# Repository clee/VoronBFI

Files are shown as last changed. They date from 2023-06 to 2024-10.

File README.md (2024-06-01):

# BFI (Beefy Front Idlers)

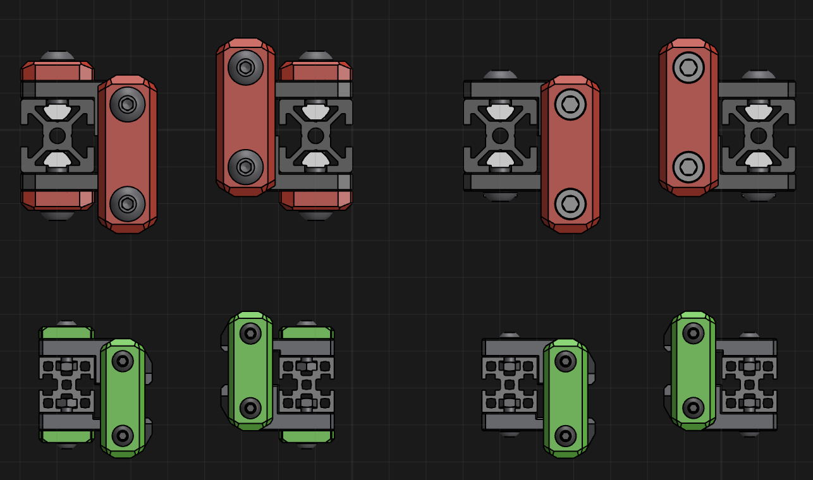
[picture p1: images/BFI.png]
BFI family render


### What?

These are replacement front idlers for Vorons (and Voron-based machines) designed with one core principle: use belt tension to *compress* printed layers instead of splitting or pulling them apart.

This design is available for Voron Trident, Voron 2.4, Salad Fork, and Micron.

### Why?

Using BFI means you should never have to deal with this kind of heartbreak again.

Stock | Rama's
--- | ---
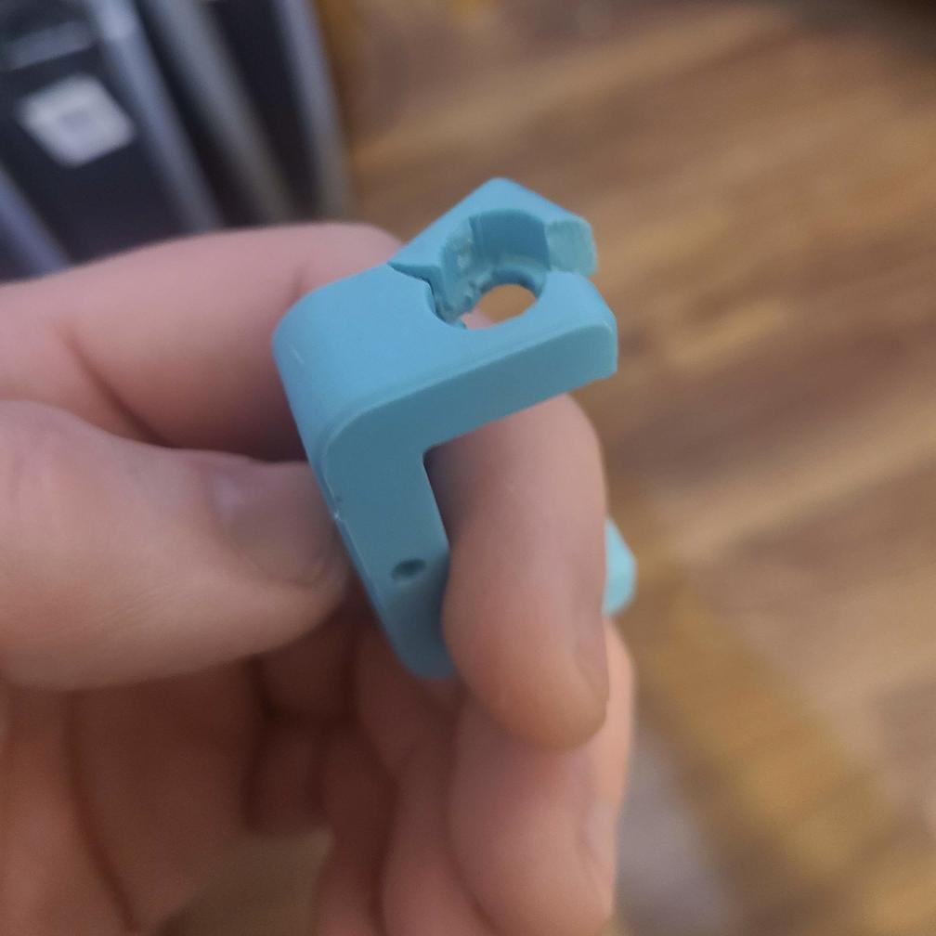
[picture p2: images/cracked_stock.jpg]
cracked stock front idler
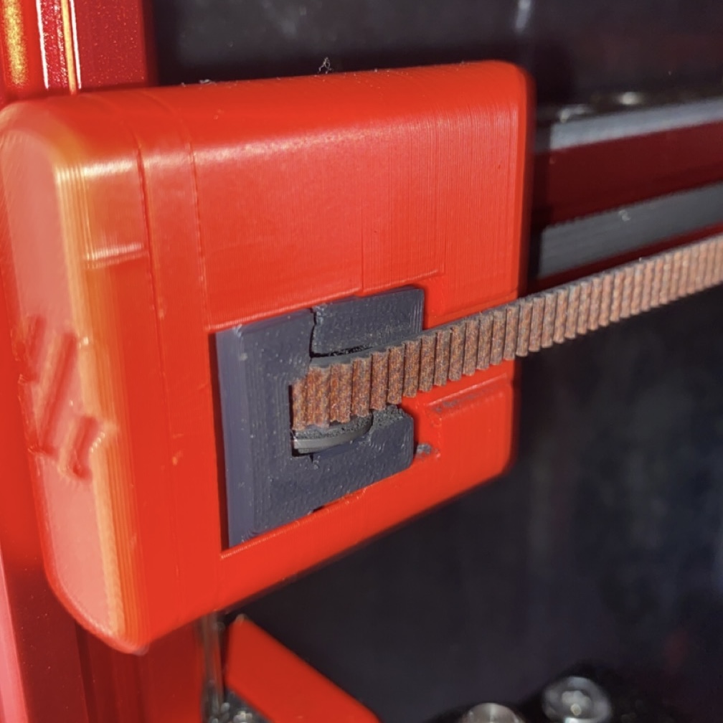
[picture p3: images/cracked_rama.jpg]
cracked Rama's front idler
 | 

## BFI for Trident

For Trident, you'll need:
- 4× M5×40 SHCS
- 4× M5 hex nuts
- 2× 5mm-diameter pin, 18mm long

...plus the same shim/bearing stack setup for each idler as the original stock front idlers.

## BFI for Voron 2.4

For V2.4, you'll need:
- 4× M5×30 BHCS 
- 4× M5 hex nuts
- 2× 5mm-diameter pin, 18mm long
- 2× M3 t-nuts
- 2× M3×16 BHCS

...plus the same shim/bearing stack setup for each idler as the original stock front idlers.

## BFI for Ants

For Salad Fork, you'll need:
- 4× M3×25 BHCS
- 4× standard Voron M3x5x4 heatset inserts (5mm outer diameter, 4mm deep)
- 2× M3×12 SHCS

For Micron, you'll need:
- 4× M3×20 BHCS
- 4× standard Voron M3x5x4 heatset inserts (5mm outer diameter, 4mm deep)
- 2× M3×12 SHCS

...plus the same shim/bearing stack setup for each idler as the original stock front idlers.

### But wait, there's more!

The same carriage design has also been applied to work with Micron, Voron 2.4, and Doomcube Z idlers.

# BZI (Beefy Z Idlers)

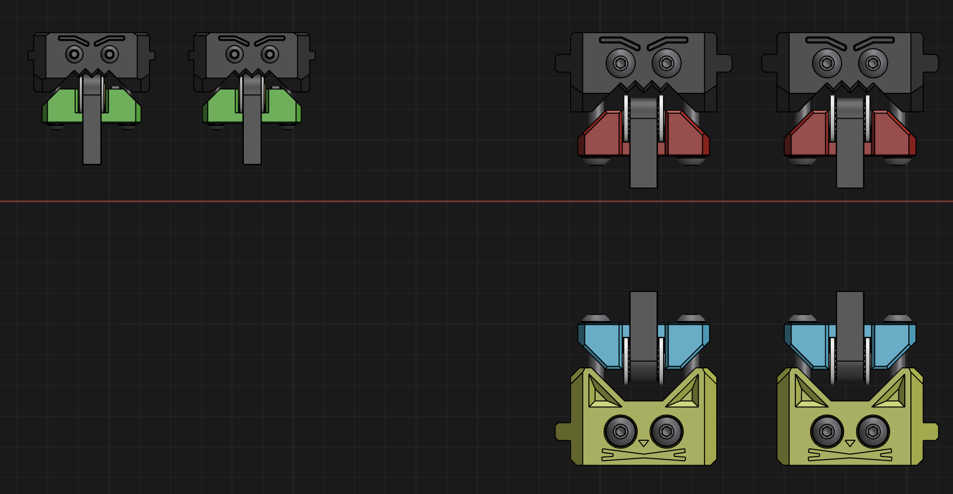
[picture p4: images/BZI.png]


## BZI for Voron 2.4

For V2.4, you'll need:
- 8× M5 hex nuts
- 8× M5×40 SHCS
- 4× 5mm-diameter pin, 22mm long

You'll reuse the existing M5×30 BHCS and roll-in M5 nuts for mounting to the frame, as well as the 20T toothed idlers from the original stock Z idlers.

## BZI for Micron

For Micron, you'll need: 
- 8× M3 hex nuts
- 8× M3×30 BHCS
- 4× M3×16 SHCS

You'll reuse the existing M3×20 BHCS and preloaded M3 hex nuts for mounting to the frame, as well as the shim/bearing stack setup from the original stock Z idlers.

## BZI for Doomcube

For Doomcube, you'll need:
- 8× M5 hex nuts
- 8× M5×40 SHCS
- 4x 5mm-diameter pin, 22mm long

You'll reuse the existing M5×25 BHCS and roll-in M5 nuts for mounting to the frame, as well as the 20T toothed idlers from the original stock Z idlers.

## One more thing

There are also a bunch of [usermods](usermods/) for BFI. If you have non-Gates idlers, or you want Voron logos, or wish BFI were more symmetrical… might want to check them out!

# Whose fault is all this anyway?

- @clee, initial prototype
- @bythorsthunder, early feedback and testing
- @KayosMaker, first port to V2.4
- @hartk1213, Micron and Doom 

While not directly built upon it, this design is definitely inspired by @Ramalama2's front idlers.

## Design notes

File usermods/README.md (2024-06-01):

# BFI user mods

### Included in this repo:

| Creator | Title | Description |
| --- | --- | --- |
|telxoid|[V2.4 & Trident Front Logos](https://github.com/clee/VoronBFI/tree/main/usermods/telxoid)| BFI Front Logos with Voron Logos and Dual colour option.|
||[V2.4 & Trident Grippy Carrier](https://github.com/clee/VoronBFI/tree/main/usermods/telxoid)| Updated carrier to allow the shaft to push from the top/bottom rather than slot in.|
|Jadecky|[BZI for Micron Pin Mod](https://github.com/clee/VoronBFI/tree/main/usermods/Jadecky/STLs/Pin%20Mod_Micron/BZI)| Pin Mod for Micron BZI.|
||[BFI for Micron Pin Mod](https://github.com/clee/VoronBFI/tree/main/usermods/Jadecky/STLs/Pin%20Mod_Micron/BFI)| Pin Mod for Micron BFI|
||[BZI for Micron Non symmetrical Bodies](https://github.com/clee/VoronBFI/tree/main/usermods/Jadecky/STLs/Non%20Symmetrical%20BZI%20Idler%20Bodies)| Removed one of the ears on the exposed side of the body, purely aesthetic.|
|LillianaMirrors|[BZI For 14mm Pulleys (Chaoticlab Idlers)](https://github.com/clee/VoronBFI/tree/main/usermods/LillianaMirrors/)| Widened the BZI idler hole for 14mm pulleys, commonly used on the 2.4 Tool-less Z Idlers|
|GiulianoM|[BZI for DoomCube 4040](./GiulianoM/)| Extended idler bodies for use with a DoomCube built with 4040 frames.|
|Mosher|[BZI Light](https://github.com/clee/VoronBFI/tree/main/usermods/Mosher/BZI%20Light%20Idlers)| Slimmed down wersion of BZI uses shorter man body screws and 2x M3 for carrier. Great variety of versions.|
|MikeYankeeOscarBeta|[9MM BFI](./MikeYankeeOscarBeta/)| 9mm BFI. Using 5x22mm pins|
|Tetsu|[Symmetrical BFI](./Tetsu/Symetrical%20BFI/)| Symmetrical BFI parts with options for M3 & M5 hardware & BFI front logos|
|DonaldSayers|[45 Degree Housing](./DonaldSayers/)| Made the housing a bit easier to print the overhang. Mostly print aesthetics.

## Other BFI forks/variants
| Creator | Title | Description |
| --- | --- | --- |
| Radiotbo | [Smooth BFI](https://github.com/Radiotbo3d/SBFI) | Smoother, more symmetrical take on BFI for V2.4 and VT |
| Diyshift | [BFI Gears](https://github.com/Diyshift/3D-Printer/tree/main/BFI%20Gears) | Allows you to adjust both M5 bolts at once for VT |

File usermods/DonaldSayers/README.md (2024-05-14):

## V2.4 Housing with 45 degree overhang.
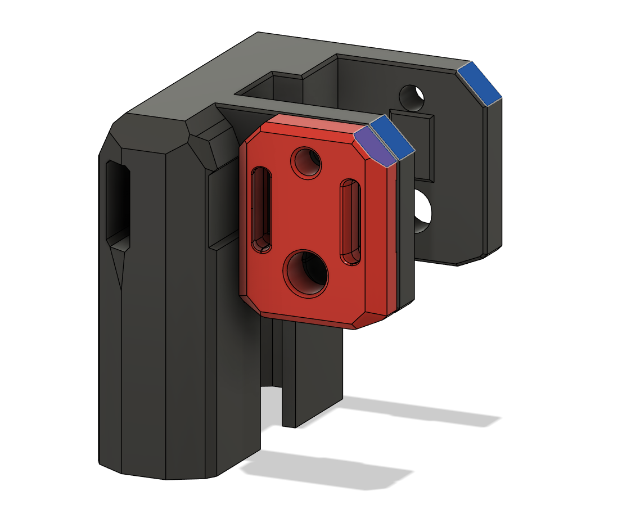
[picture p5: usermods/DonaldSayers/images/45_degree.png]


The angle on the housing was really steep. I cut it off and blended it with a chamfer to blend it in. It does make the default belt holder overhang on the back so I've added the same geometry to work with both A and B.

Mostly for print aesthetics.

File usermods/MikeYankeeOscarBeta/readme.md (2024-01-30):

## MikeYankeOscarBeta  Voron 2.4 9mm BFI for 9mm belts and 5x22mm pins
#### VoronDesign-Discord: MikeyMike V2.5796

Made to fit with the 9mm Belt mod XY idlers and AB stepper mounts found here: 
https://www.printables.com/model/485237-voron-24-9mm-gantry 
(which might also be this project on github: https://github.com/Sneeky-Pete/Fatso)

These replace the 9mm ramalama2 front idlers in the Etretti Voron 2.4 9mm gantry

## BFI 9mm belt mod for Voron 2.4

For V2.4 9mm BFI, you'll need:
- 4× M5×30 BHCS 
- 4× M5 hex nuts
- 2× 5mm-diameter pin, 22mm long
- 2× M3 t-nuts
- 2× M3×16 BHCS (i think, but might need longer)

...plus the 14mm shim/bearing stack setup for each idler, same as the 9mm belt mod front idlers.

## Kudos to the voron community, and especially:  
- clee for the BFI BZI mod
- Etretti &&|| Sneeky-Pete for the 9mm mod
- Johan/Alucardi V2.12171 V0.1479 for breaking his 9mm ramalama2 idlers

## Changelog:
- 20230910: initial version

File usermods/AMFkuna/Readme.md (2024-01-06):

Modified version of [telxoid](https://github.com/clee/VoronBFI/tree/main/usermods/telxoid) usermod of BFI for V2.4/Trident

M3 heat inserts and M3 fasteners for fine tunning

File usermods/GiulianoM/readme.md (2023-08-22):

# BZI Frame for DoomCube 4040
I'm making a DoomCube 2.4 variant with 4040 extrusions for the frame.

These are extended idler bodies to take advantage of the deeper 4040 extrusions.

They have a Cat *and* a Bird on them.

Modifications:
* Hex nuts are now in the middle of the body.
* You'll need 2x M5 50mm BHCS instead of 40mm.
* You'll need 2x extra M5 Roll In nuts and 2x extra M5 25mm BHCS.

## Pictures

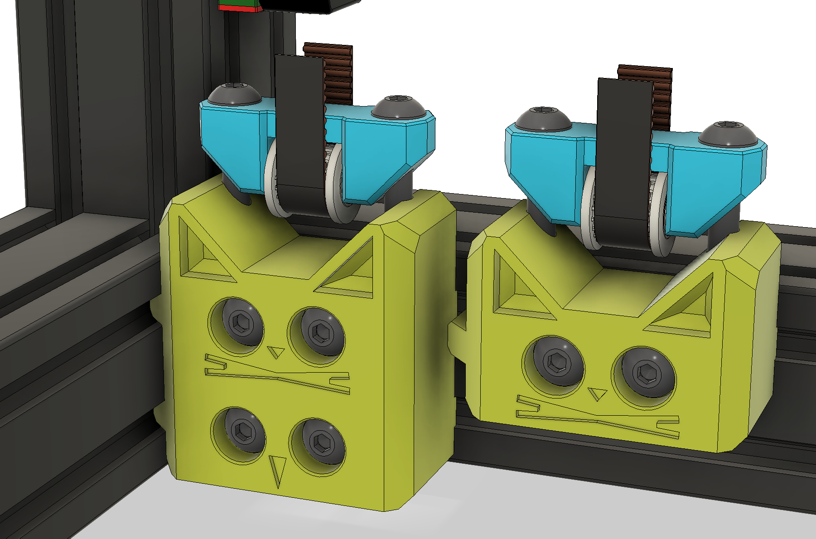
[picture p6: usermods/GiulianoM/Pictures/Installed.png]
Meow Meow


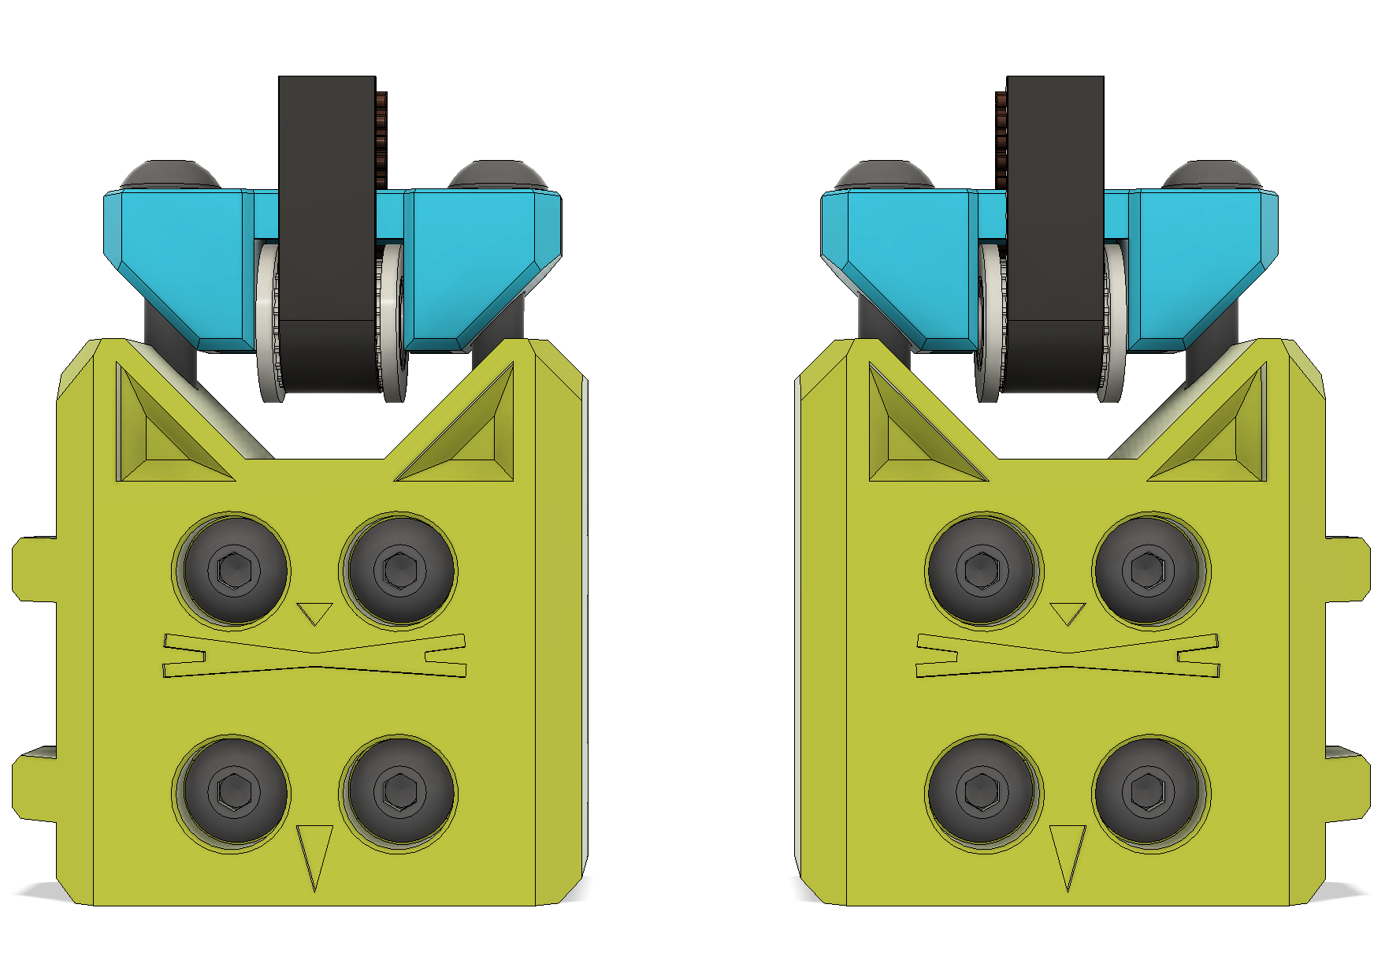
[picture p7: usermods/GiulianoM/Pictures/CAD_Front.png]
Meow Meow SQUAWK


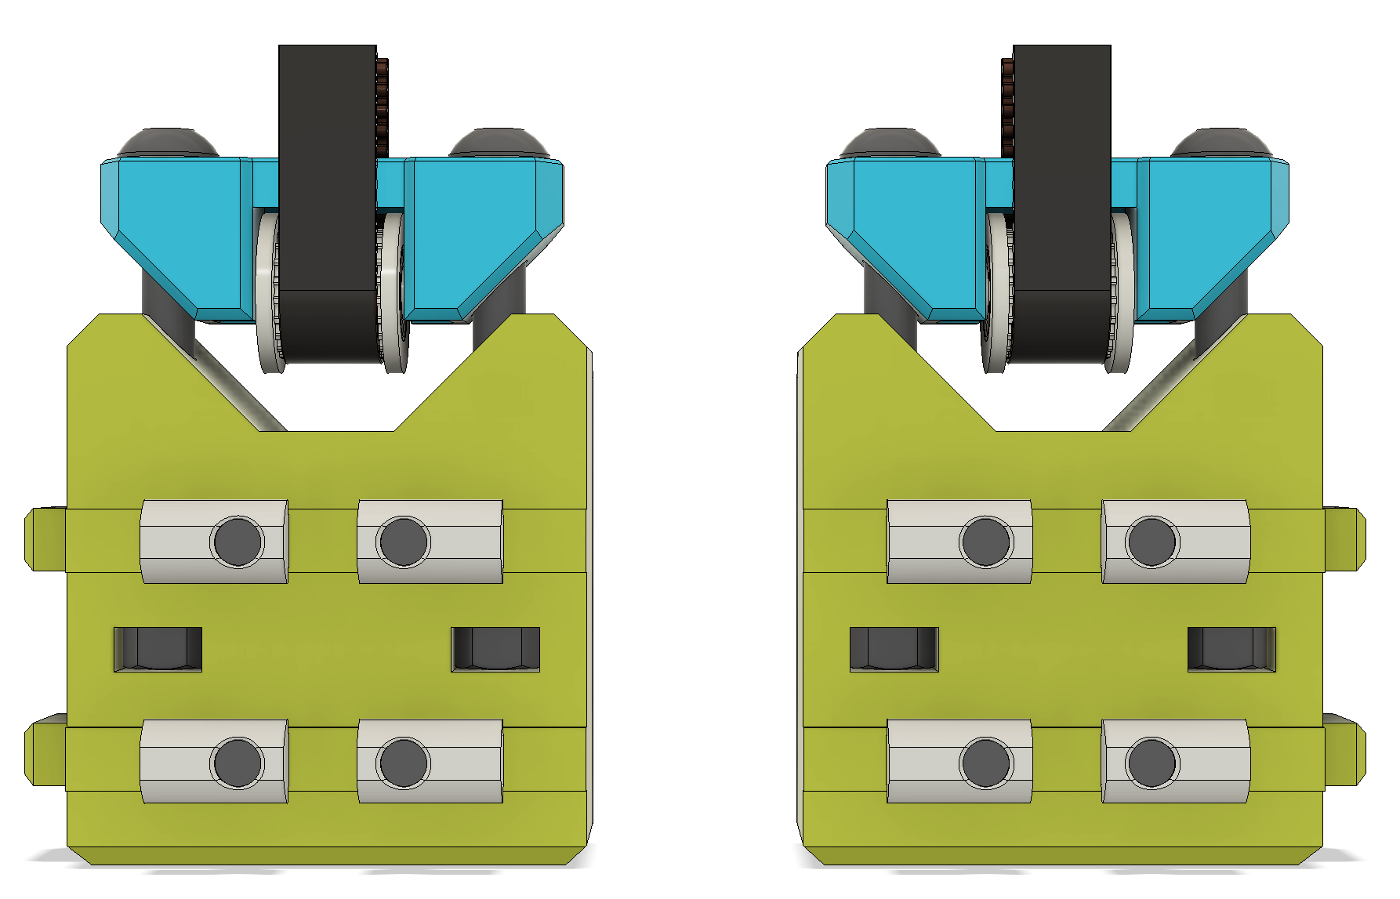
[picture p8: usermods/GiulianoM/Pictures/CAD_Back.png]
CAT BUTT


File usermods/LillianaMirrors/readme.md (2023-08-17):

# BZI for 14mm Pulleys (ChaoticLab Tool-less Z idler)

A simple little replacement for the lower idler holder. 

The fasteners are all the same, just a wider carrier.

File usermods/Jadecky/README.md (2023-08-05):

#### Thanks to HartK for the orignal Pin Mod, and Staticanime for testing and feedback on these mods.

## [BZI for Micron Pin Mod](https://github.com/clee/VoronBFI/tree/main/usermods/Jadecky/STLs/Pin%20Mod_Micron/BZI)

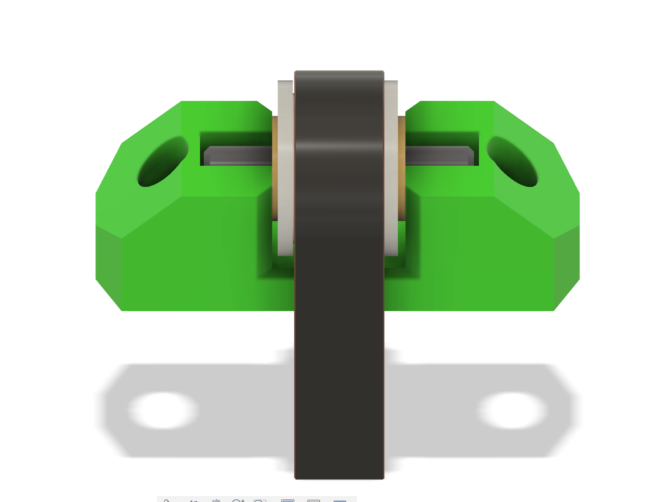
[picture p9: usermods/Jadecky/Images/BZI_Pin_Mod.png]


Pin mod for Micron BZI.

Replaces:

- ```4× M3×12 SHCS``` 

with:

- ```4x 3x18mm Pins```

I ground down my original 3x20mm pins from the original Micron Pin Mod.

## [BFI for Micron Pin Mod](https://github.com/clee/VoronBFI/tree/main/usermods/Jadecky/STLs/Pin%20Mod_Micron/BFI)

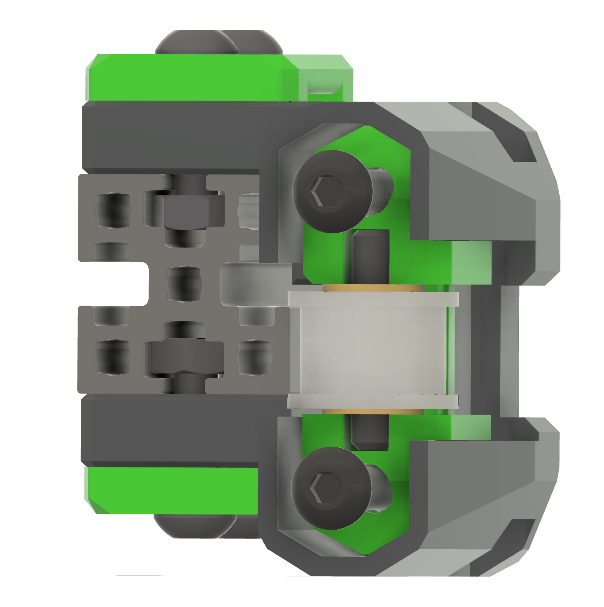
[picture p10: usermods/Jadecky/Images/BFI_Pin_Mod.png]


Pin mod for Micron BFI.

Replaces:

-```2x M3x12SHCS```

with:

-```2x 3x15mm Pins```

## [Non Symmetrical Bodies](https://github.com/clee/VoronBFI/tree/main/usermods/Jadecky/STLs/Non%20Symmetrical%20BZI%20Idler%20Bodies)

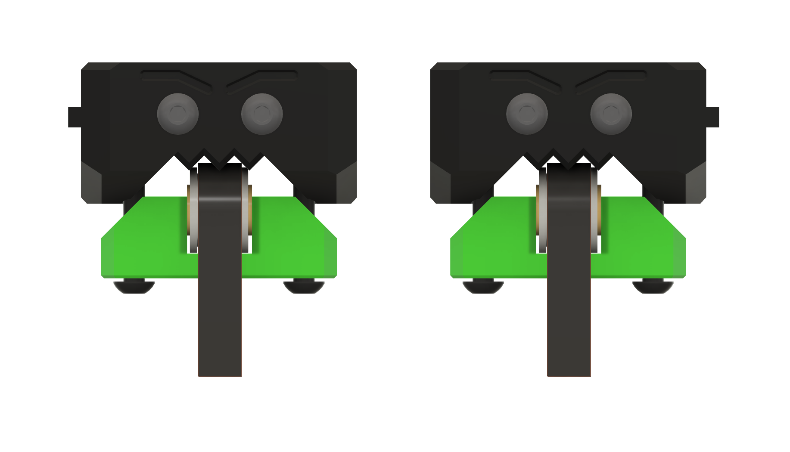
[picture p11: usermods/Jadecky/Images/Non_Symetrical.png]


I've removed one of the 'ears' from the bodies, to make it more in line with the original Z Tensioners from the Micron. Purely an aesthetic mod that satisfies my OCD.

You'll need:

- 2x ```Idler_Body_L.stl```
- 2x ```Idler_Body_R.stl```

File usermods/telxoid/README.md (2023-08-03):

## V2.4 / Trident Fronts with Logos
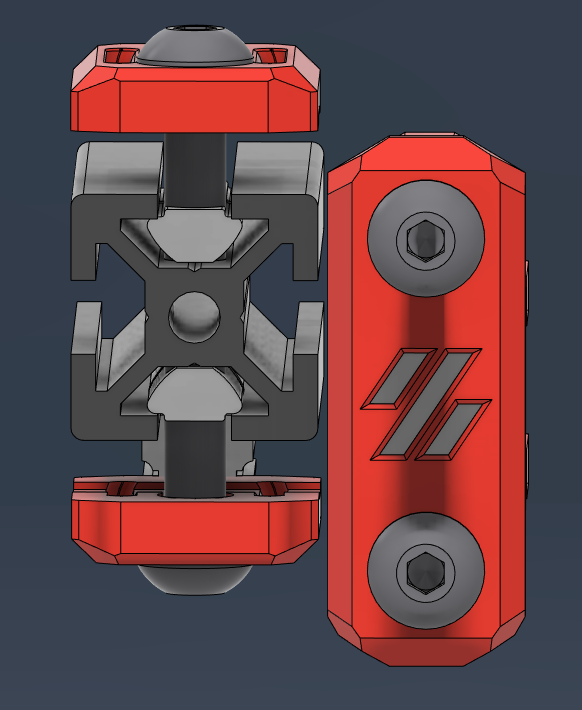
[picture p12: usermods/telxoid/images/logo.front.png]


Added dual color logo option for front plate.  If you just want a logo, print both the same color and slip them together. Meant to push together with no glue, but add a drop if you're paranoid or underextrude for fun.  Works on V2/VT

## V2.4 / Trident Grippy Carrier 
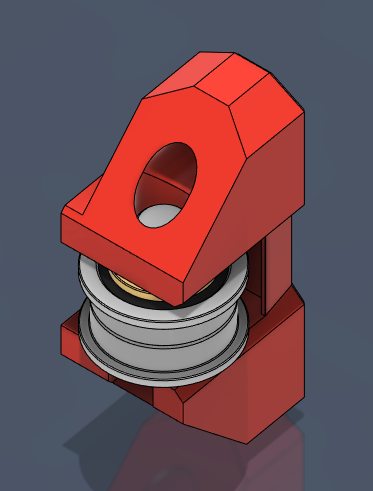
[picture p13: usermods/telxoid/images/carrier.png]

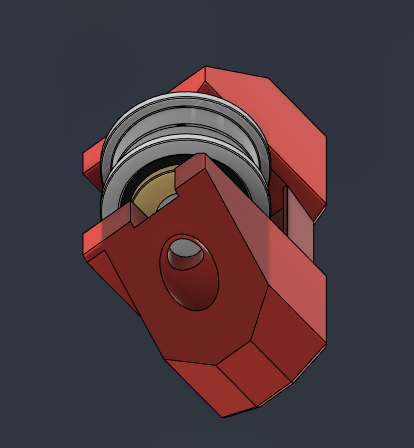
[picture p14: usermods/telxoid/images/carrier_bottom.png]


Updated carrier to allow the shaft to push from the top/bottom rather than slot in, as I was having issues keeping the shaft and bearings together during assembly.  Also provides a bit more give in shaft length for those like me that cut their own.  This will give up about 2mm in travel.  Hole in the bottom to a push the shaft back out when the time comes.  Works on V2/VT

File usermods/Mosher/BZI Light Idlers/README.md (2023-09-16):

Light version of the BZI Idlers.
- Slimmed down main body, uses 2x M5x20mm instead of M5x30mm
- Heat insert version
- Two color version
- Countersunk version
- Versions for 5mm and 6mm Profiles
- Carrier uses 2x M3x40mm instead of M5x40mm
- Carrier for 20mm and 22mm shafts 





Note: countrersunk M3 carrier hasn't been tested yet.

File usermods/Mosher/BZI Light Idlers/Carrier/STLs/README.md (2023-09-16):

4 Versions: for either 20 or 22 mm pin/shaft and either for BHSC/SHSC or countersunk screws

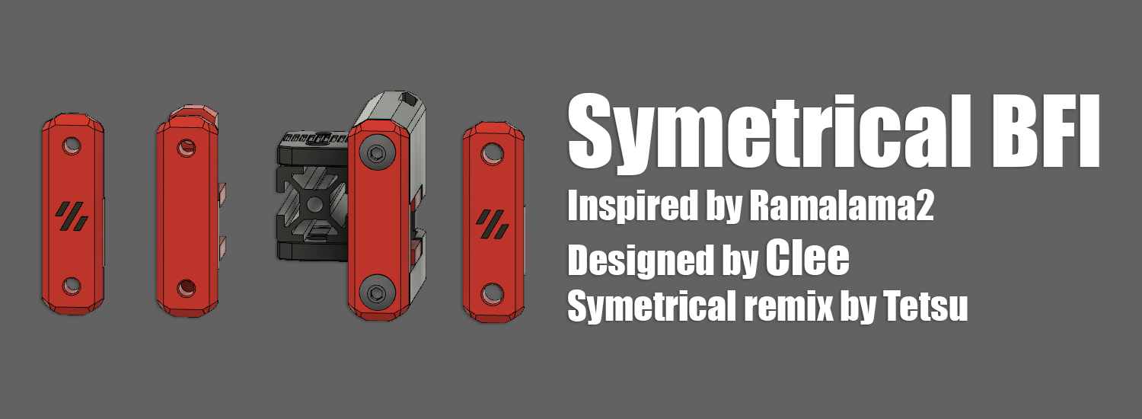
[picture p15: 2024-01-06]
usermods/Tetsu/Symmetrical BFI/images/hlavicka.png

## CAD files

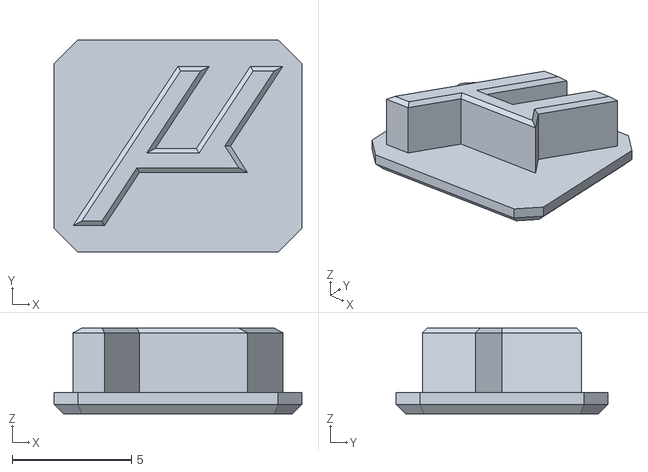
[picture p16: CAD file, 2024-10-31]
STLs/Micron/BFI/bfi_logo_insert_x2.stl
10.4 x 8.89 x 3.60

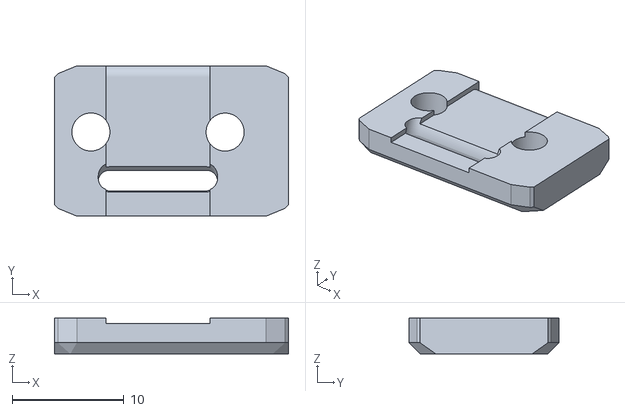
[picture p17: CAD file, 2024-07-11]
STLs/Micron/BZI/BearingStacks/[a]_top_z_belt_clamp_x2.stl
20.9 x 13.4 x 3.20

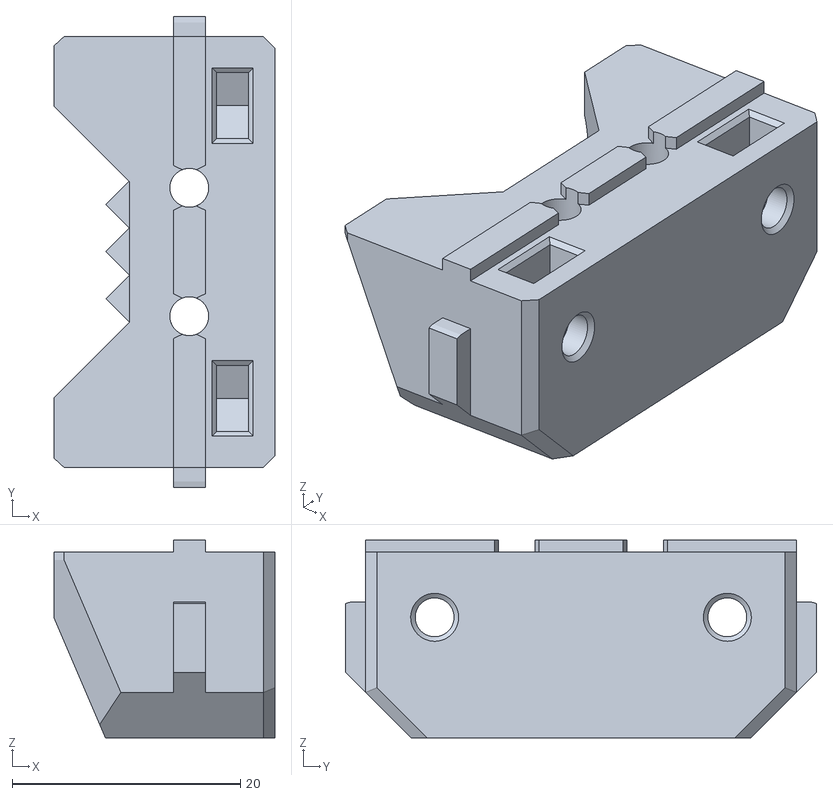
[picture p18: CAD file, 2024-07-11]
STLs/Micron/BZI/BZI_micron_idler_body_x4.stl
19.3 x 41.3 x 17.4

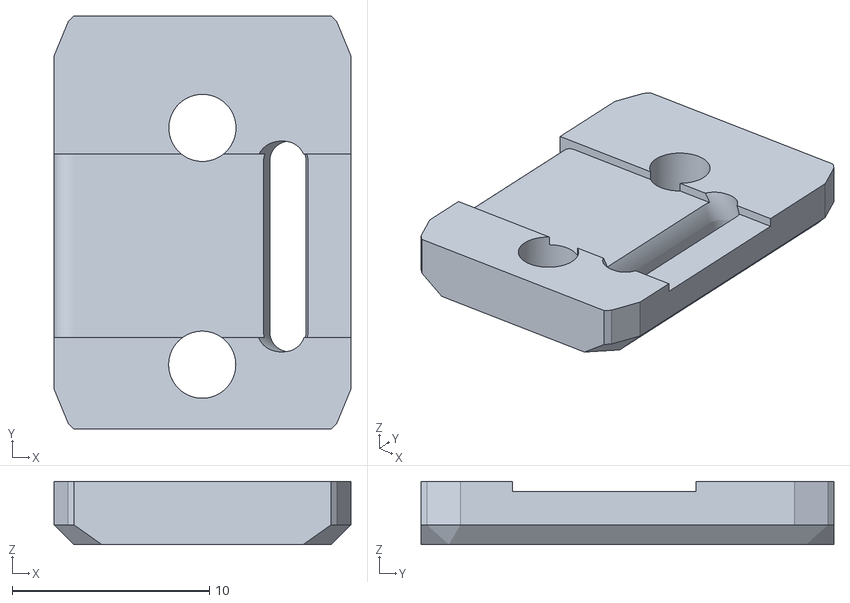
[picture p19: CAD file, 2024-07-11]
STLs/Micron/BZI/ToothedIdler/[a]_z_belt_clamp_x4.stl
15.0 x 20.9 x 3.20

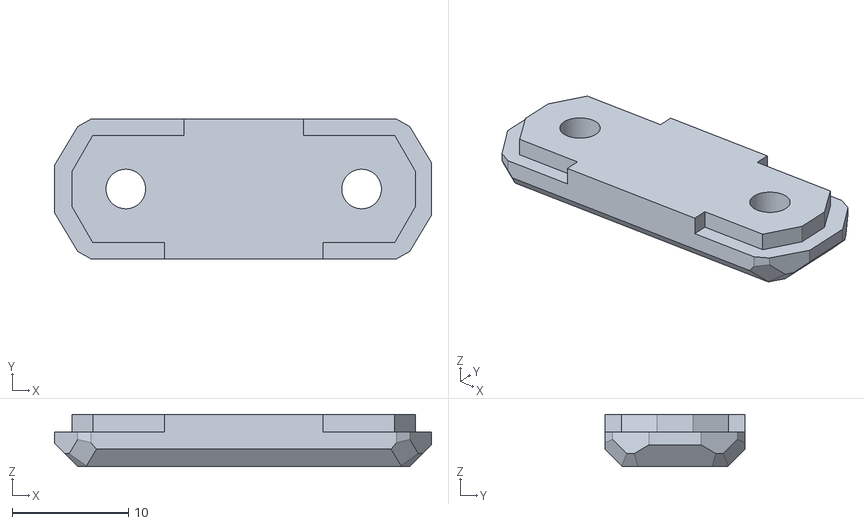
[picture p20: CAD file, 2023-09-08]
STLs/SaladFork/[a]_BFI-SaladFork_Front_x2.stl
32.4 x 12.0 x 4.50

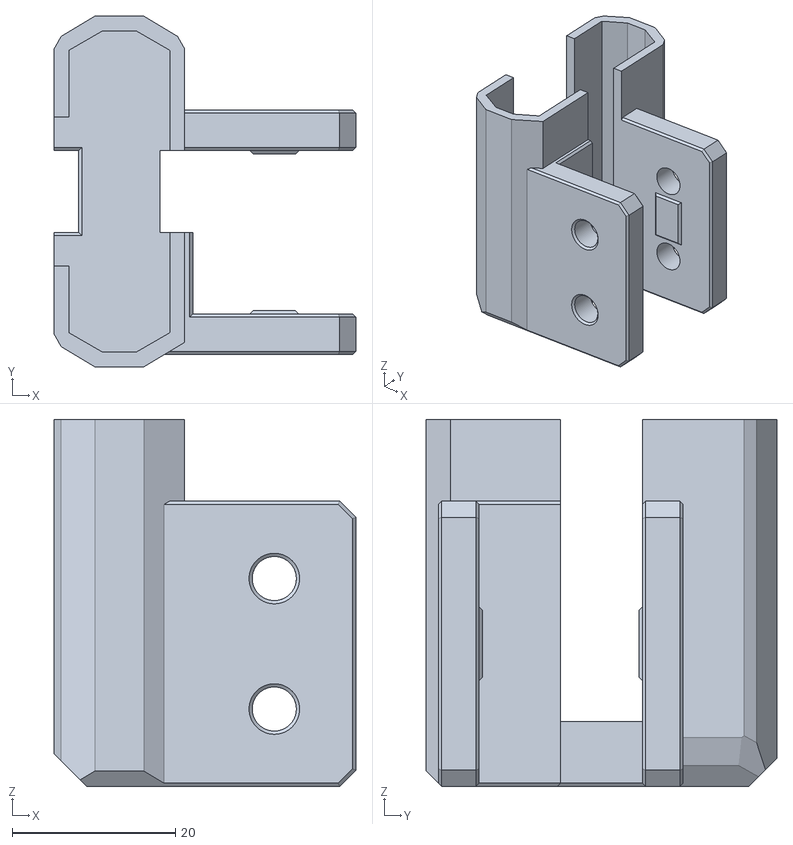
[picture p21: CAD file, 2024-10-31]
STLs/Trident/BFI-VT_Housing_x2.stl
37.0 x 43.0 x 45.0

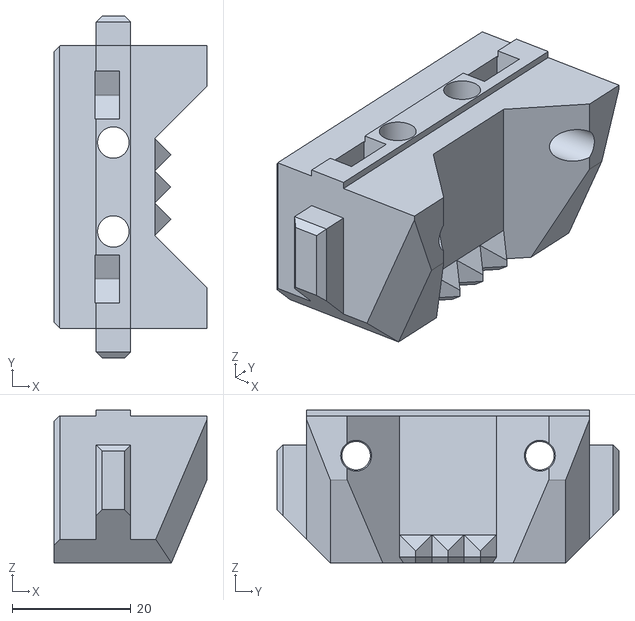
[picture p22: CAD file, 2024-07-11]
STLs/V2/BZI/BZI_V2.4_idler_body_x4.stl
25.8 x 57.7 x 25.8

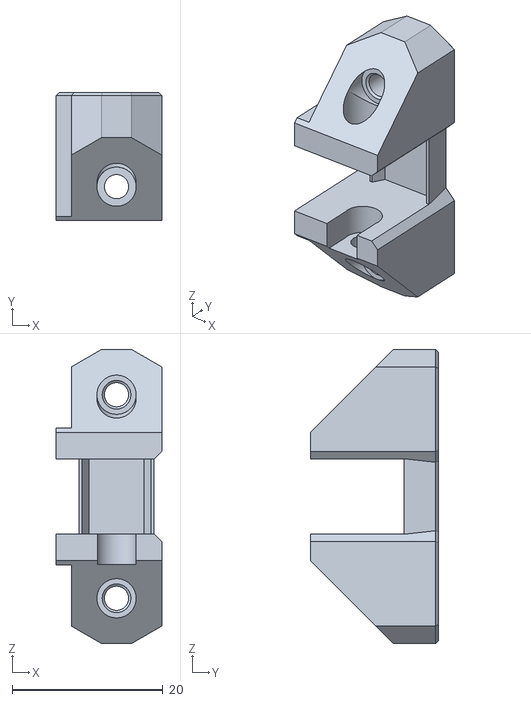
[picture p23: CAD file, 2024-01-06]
usermods/AMFkuna/BFI_V2_VT_Grippy_Carrier M3.stl
14.0 x 17.0 x 39.0

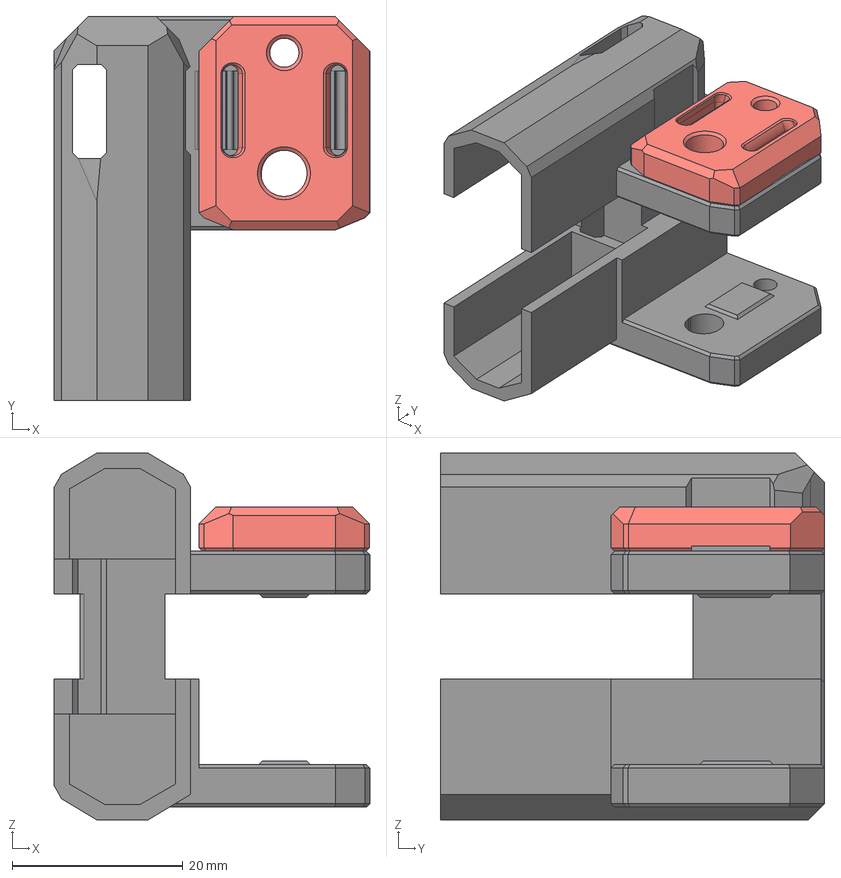
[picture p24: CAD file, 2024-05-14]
usermods/DonaldSayers/CAD/BFI V2.4 better printability 45 degree.step
37.0 x 45.0 x 43.0 mm
V2_Belt_Clamp
V2_Housing (1)

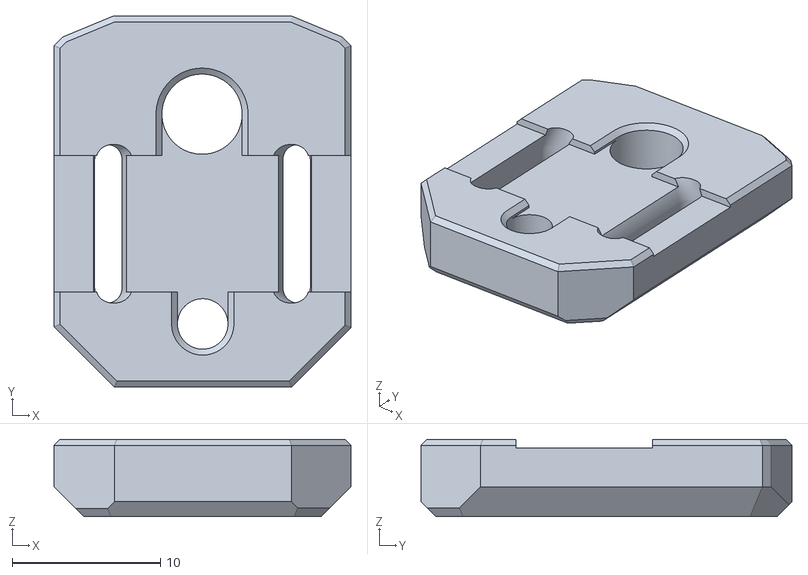
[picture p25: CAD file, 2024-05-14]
usermods/DonaldSayers/STL/[a] 45d-V2.4_Belt_Clamp_x4.stl.stl
20.0 x 25.0 x 5.20

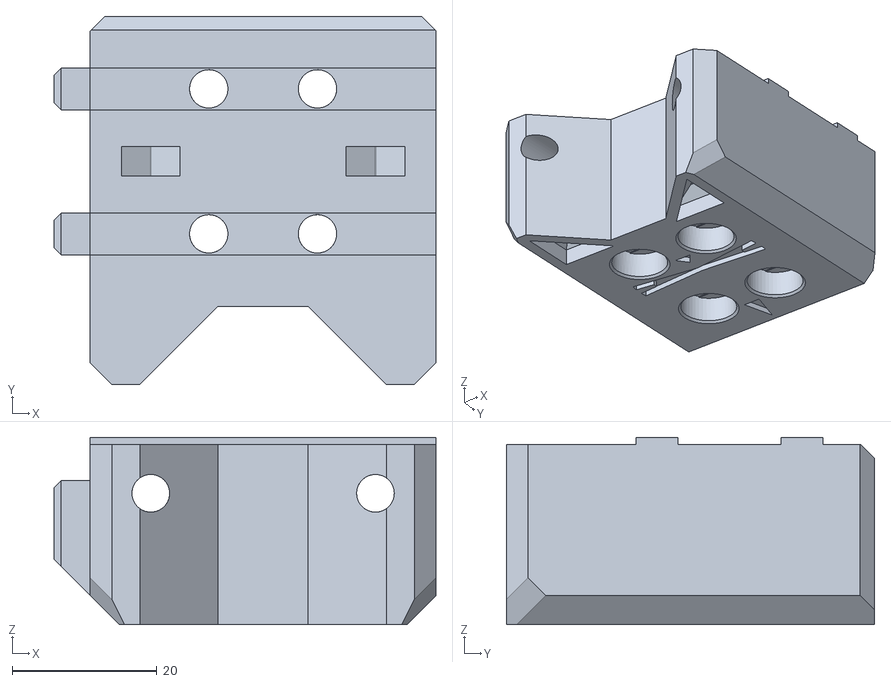
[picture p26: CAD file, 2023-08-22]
usermods/GiulianoM/STLs/BZI_DoomCube_4040_Idler_Body_A.stl
52.7 x 50.8 x 25.8

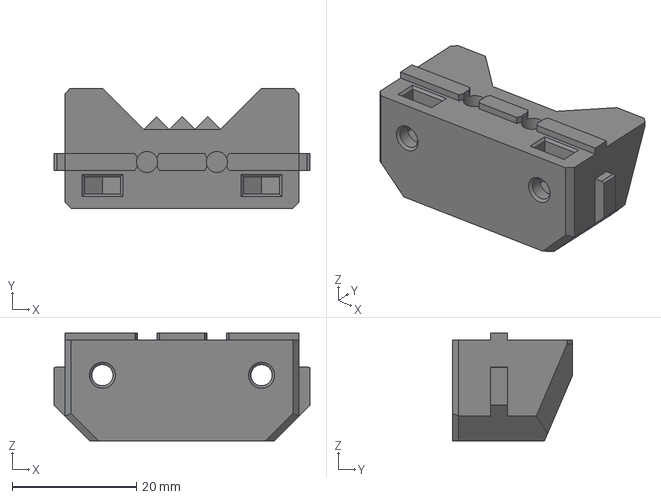
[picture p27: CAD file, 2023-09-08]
usermods/hartk/CounterSunk_MicronBZI/CAD/Micron_BZI_CounterSunk_Spacer.step
41.3 x 19.3 x 17.4 mm

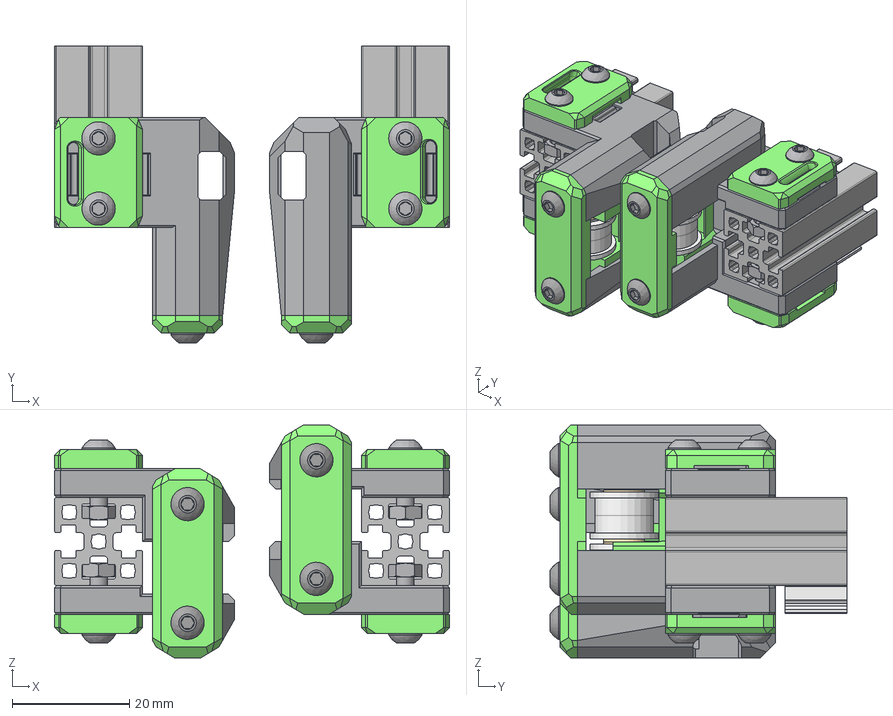
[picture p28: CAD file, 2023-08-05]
usermods/Jadecky/CAD/BFI_Micron_Pin_Mod.step
67.4 x 50.6 x 39.8 mm
F623-2RS:2 (2)
3x15mm Pin
M3 Washer 7mmx.5mm:2 (2)
M3 Washer 7mmx.5mm:1 (2)
F623-2RS:1 (2)
M3x20 BHCS:1
M3x20 BHCS:2
M3x12 BHCS:2
M3 HexNut:1
M3 HexNut:2
M3x12 BHCS:4
M3x12 BHCS:3
M3 HexNut:3
M3 HexNut:4
M3x12 BHCS:1
MGN7:1 (2)
Micron_Front_Idler_Housing:1
Micron_SF_Front_Idler_Carrier:1
Micron_SF_Front_Idler_Front_Cover:1
Upper:1
Lower:1
F623-2RS:2 (3)
3x15mm Pin (1)
M3 Washer 7mmx.5mm:2 (3)
M3 Washer 7mmx.5mm:1 (3)
F623-2RS:1 (3)
M3x20 BHCS:1 (1)
M3x20 BHCS:2 (1)
M3x12 BHCS:2 (1)
M3 HexNut:1 (1)
M3 HexNut:2 (1)
M3x12 BHCS:4 (1)
M3x12 BHCS:3 (1)
M3 HexNut:3 (1)
M3 HexNut:4 (1)
M3x12 BHCS:1 (1)
MGN7:1 (3)
Micron_Front_Idler_Housing:1 (1)
Micron_SF_Front_Idler_Carrier:1 (1)
Micron_SF_Front_Idler_Front_Cover:1 (1)
Lower:1 (1)
Lower:1 (2)

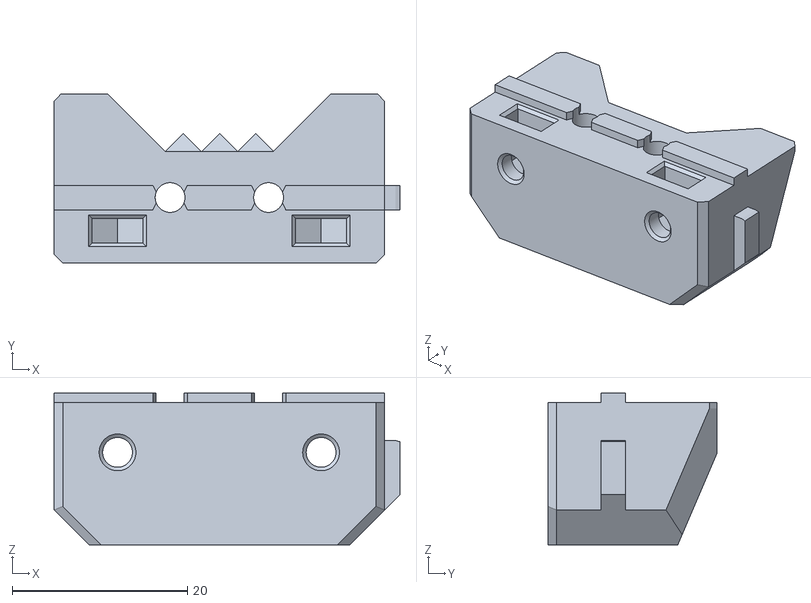
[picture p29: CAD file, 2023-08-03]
usermods/Jadecky/STLs/Non Symmetrical BZI Idler Bodies/Idler_Body_L_x2.stl
39.5 x 19.3 x 17.4

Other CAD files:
STLs/V2/BFI/BFI-V2.4_Housing_x2.stl
usermods/hartk/CounterSunk_MicronBZI/STLs/Micron_BZI_CounterSunkSpacer_MMU.stl
usermods/Jadecky/STLs/Pin Mod_Micron/BFI/[a]_Front_Idler_Pin_Mod_x2.stl
usermods/Jadecky/STLs/Pin Mod_Micron/BZI/[a]_Idler_Carrier_Pin_Mod_x4.stl
STLs/Micron/BFI/[a]_front_cover_logo_x2.stl
STLs/Micron/BFI/[a]_front_cover_x2.stl
STLs/Micron/BFI/[a]_idler_carrier_x2.stl
STLs/Micron/BFI/idler_housing_x2.stl
STLs/Micron/BZI/BearingStacks/[a]_bottom_z_belt_clamp_mirror_x2.stl
STLs/Micron/BZI/BearingStacks/[a]_top_z_belt_clamp_mirror_x2.stl
STLs/Micron/BZI/BearingStacks/[a]_z_idler_carrier_bearing_stacks_x4.stl
STLs/Micron/BZI/ToothedIdler/[a]_z_belt_clamp_mirror_x4.stl
STLs/Micron/BZI/ToothedIdler/[a]_z_idler_carrier_x4.stl
STLs/SaladFork/BFI-SaladFork_Housing_x2.stl
STLs/SaladFork/[a]_BFI-SaladFork_Carrier_x2.stl
STLs/Trident/[a]_BFI-VT_Carrier_BHCS_x2.stl
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

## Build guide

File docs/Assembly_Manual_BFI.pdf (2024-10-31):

# ASSEMBLY MANUAL

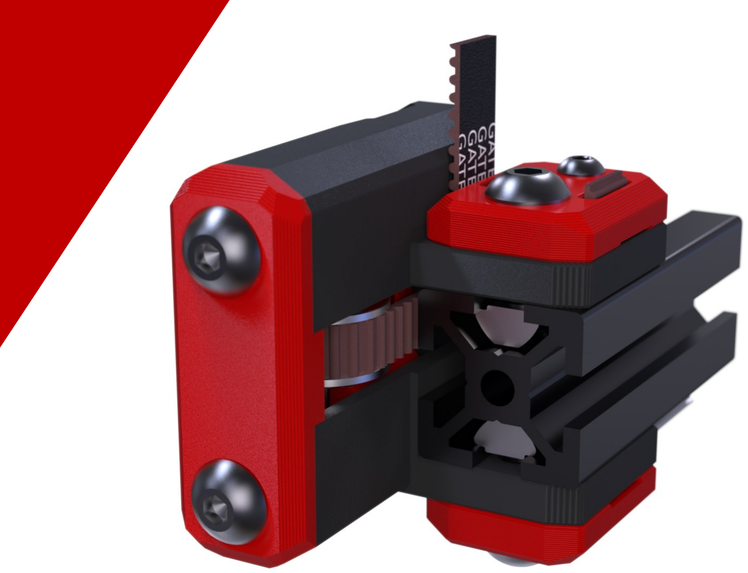
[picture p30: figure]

### Everyone could use a little extra Beef

# BFI

## VERSION 10/31/2024

## STL FILE KEY

## PRINT GUIDELINES

The STL naming convention used for BFI/BZI is the same as that used for VORON printers:

The recommended print settings are also those used for VORON printers:

### PRIMARY COLOR

Example
z_drive_main_a_x2.stl

These files will have nothing at the start of the filename.

### ACCENT COLOR

Example
[a]_z_motor_mount_a_x2.stl

These files will have ‘’[a]’’ to the front to mention that they are intended to be printed with an accent color.

### QUANTITY REQUIRED

Example
[a]_z_motor_mount_a_x2.stl

If a file ends with ‘’_x#’’, that is telling you the quantity of that part required to build this system.

FDM MATERIAL
BFI was designed for ABS.
Use other plastics at your own discretion.
LAYER HEIGHT
Recommended : 0.2mm
EXTRUSION WIDTH
Recommended : Forced 0.4mm

### INFILL PERCENTAGE

Recommended : 40%
INFILL TYPE
Grid, Gyroid, Honeycomb,
Triangle, Cubic, Adaptive Cubic. WALL COUNT
Recommended : 4
INTRODUCTION | BFI

SOLID TOP/BOTTOM LAYERS
Recommended : 5
SUPPORTS REQUIRED
Nah.

DISCO? OH …DISCORD
If you need assistance with your BFI assembly, you can head over to the Voron Discord server (https://discord.gg/voron) and post your questions (typically in the #voronuser_mods channel).

GIT GUD
If you want to keep up with the latest updates (or if you come up with a cool usermod) for BFI, the GitHub page (https://github.com/clee/VoronBFI) is the only source for the latest files.
HARDWARE - REFERENCES | BFI

## HOW TO GET HELP

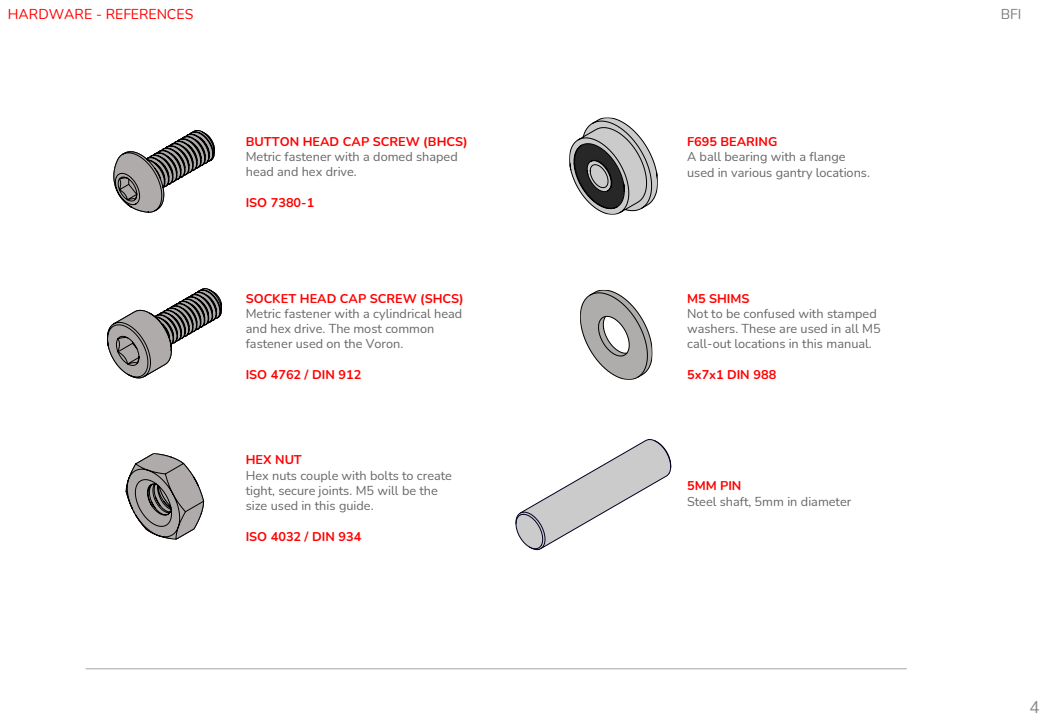
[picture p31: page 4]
HARDWARE - REFERENCES; BFI

BUTTON HEAD CAP SCREW (BHCS)
Metric fastener with a domed shaped
head and hex drive.
ISO 7380-1

F695 BEARING
A ball bearing with a flange
used in various gantry locations.

SOCKET HEAD CAP SCREW (SHCS)
Metric fastener with a cylindrical head
and hex drive. The most common
fastener used on the Voron.
ISO 4762 / DIN 912

M5 SHIMS
Not to be confused with stamped
washers. These are used in all M5
call-out locations in this manual.
5x7x1 DIN 988

HEX NUT
Hex nuts couple with bolts to create
tight, secure joints. M5 will be the
size used in this guide.
ISO 4032 / DIN 934

5MM PIN
Steel shaft, 5mm in diameter

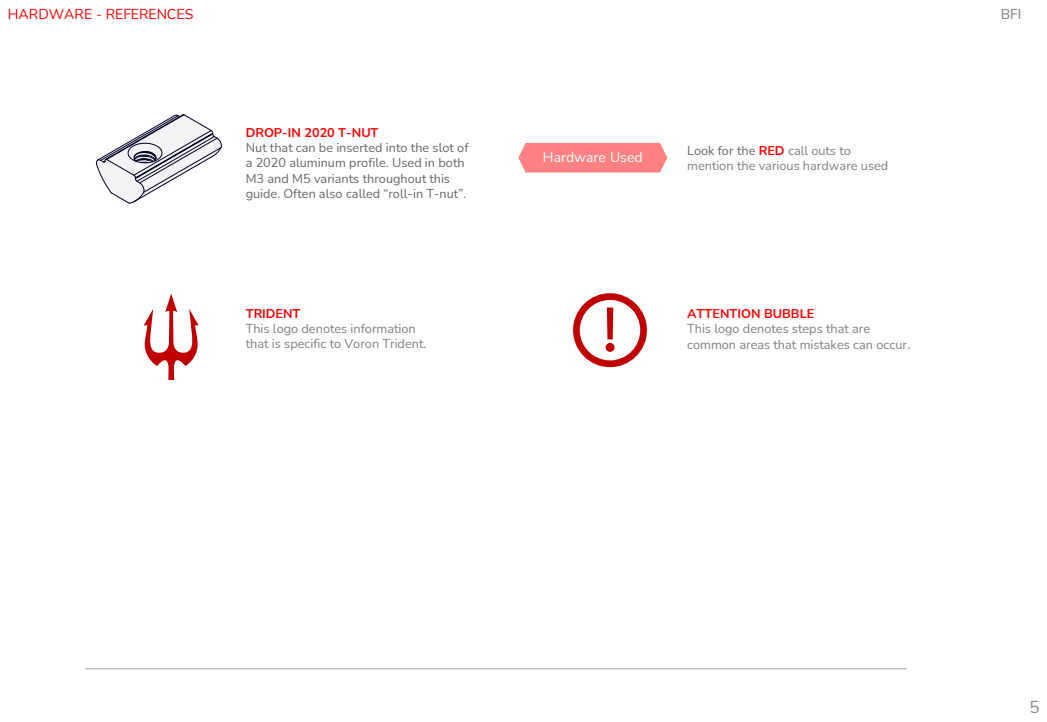
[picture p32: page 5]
HARDWARE - REFERENCES; BFI; Hardware Used; Look for the RED call outs to

DROP-IN 2020 T-NUT
Nut that can be inserted into the slot of
a 2020 aluminum profile. Used in both
M3 and M5 variants throughout this
guide. Often also called “roll-in T-nut”.

mention the various hardware used

TRIDENT
This logo denotes information
that is specific to Voron Trident.

ATTENTION BUBBLE
This logo denotes steps that are
common areas that mistakes can occur.

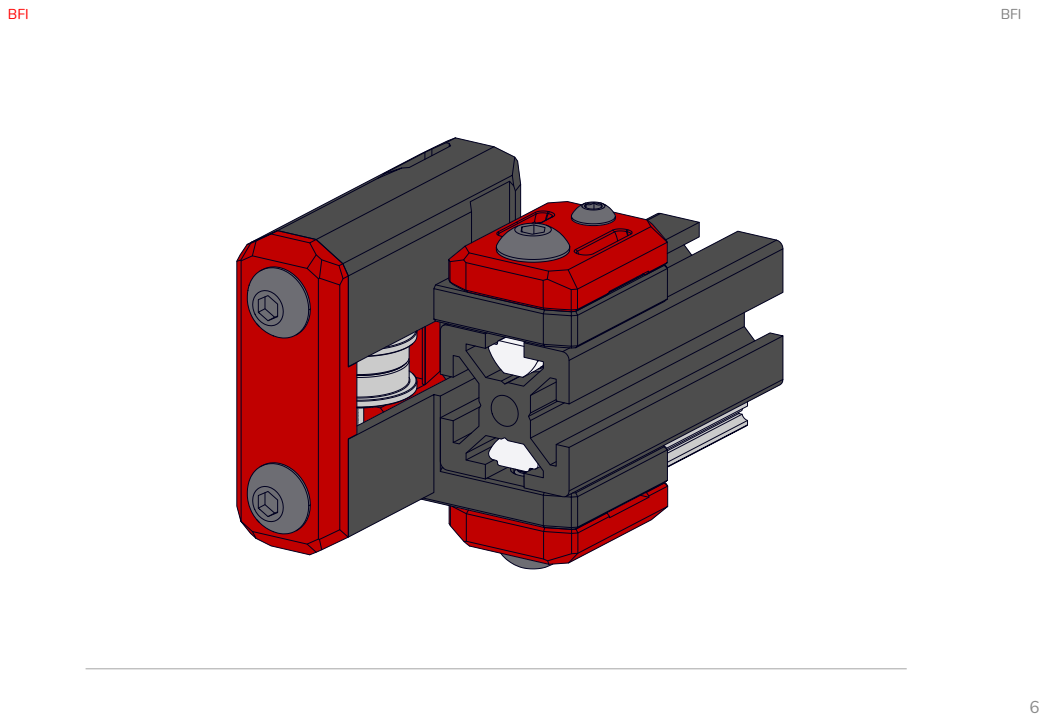
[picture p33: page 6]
BFI

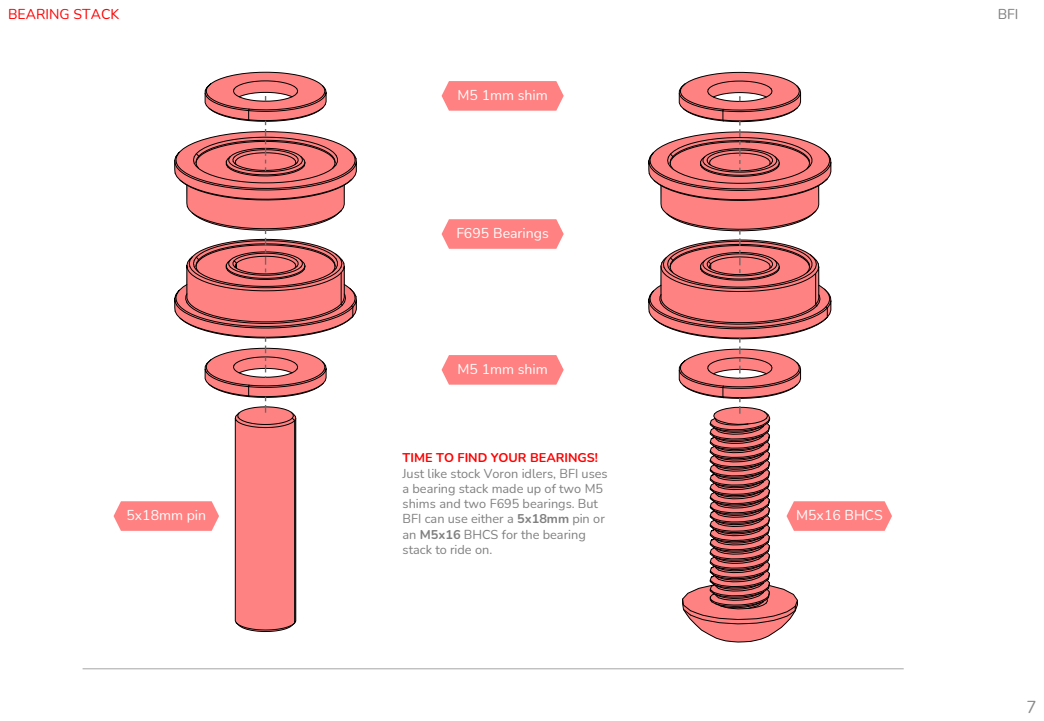
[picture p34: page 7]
BEARING STACK; BFI; 5x18mm pin; M5x16 BHCS; M5 1mm shim; F695 Bearings

TIME TO FIND YOUR BEARINGS!
Just like stock Voron idlers, BFI uses
a bearing stack made up of two M5
shims and two F695 bearings. But
BFI can use either a 5x18mm pin or
an M5x16 BHCS for the bearing
stack to ride on.

CARRIER ASSEMBLY | BFI

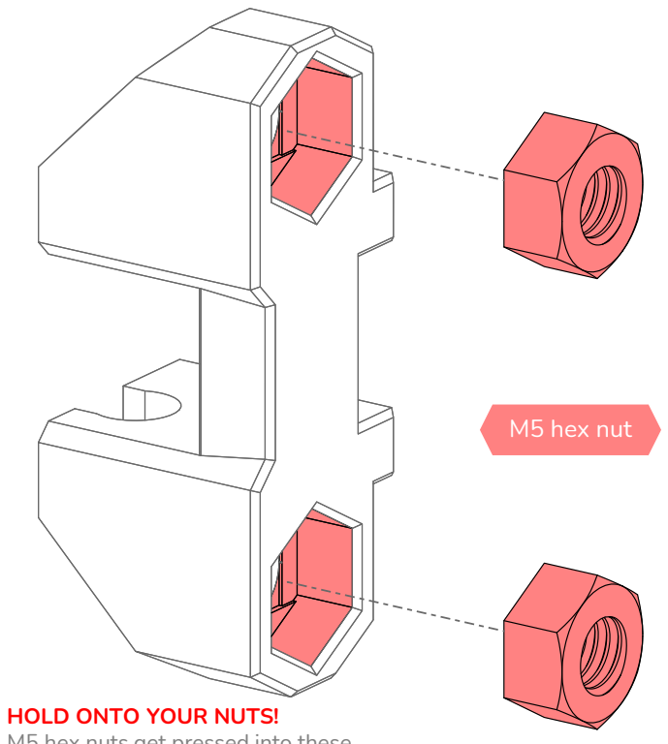
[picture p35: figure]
M5 hex nut; HOLD ONTO YOUR NUTS!

M5 hex nuts get pressed into these recesses in the back of the main body. Belt tension should prevent them from falling out once installed.

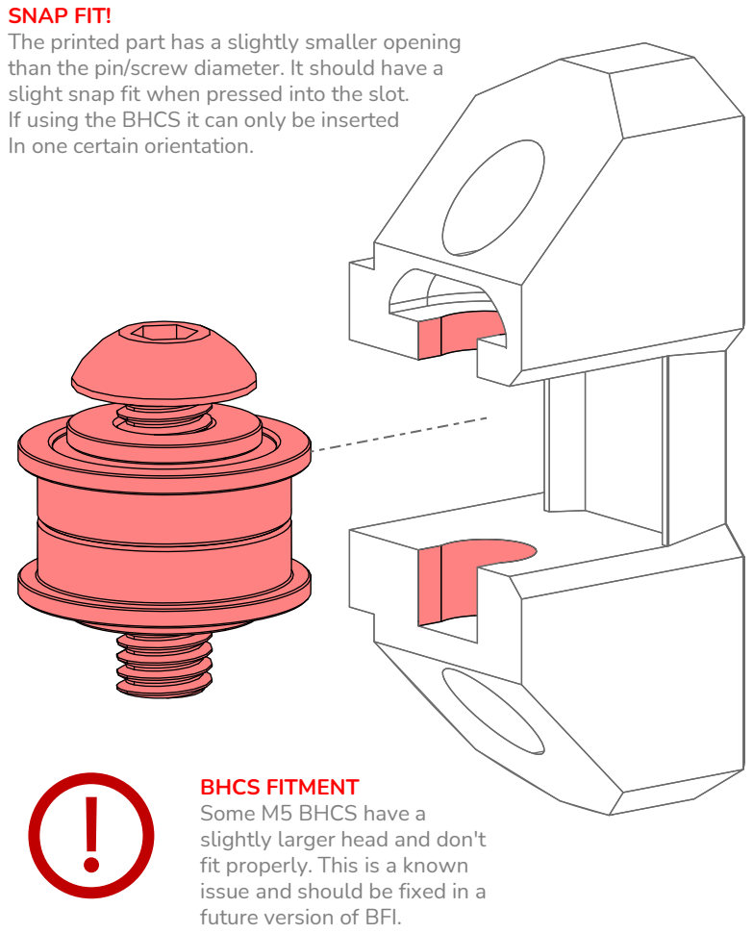
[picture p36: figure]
SNAP FIT!; In one certain orientation.; BHCS FITMENT Some M5 BHCS have a slightly larger head and don't fit properly. This is a known issue and should be fixed in a future version of BFI.

The printed part has a slightly smaller opening than the pin/screw diameter. It should have a slight snap fit when pressed into the slot.
If using the BHCS it can only be inserted

LOOSE BOLTS?
If the tensioner bolts seem to work loose, you can use a small amount of Loctite on the inside of the M5 hex nuts.

CARRIER INSTALLATION | BFI

CARRIER INSTALLATION
The carrier can only fit in the housing a specific way. The slots on the side are different sizes; make sure to line up the correct side of the carrier with the body.

WHERE'S THE TRIDENT?!
Even though this manual is only showing the V2.4 BFI installation, the assembly process and installation process is nearly identical, except for the Z belts on the V2.4.

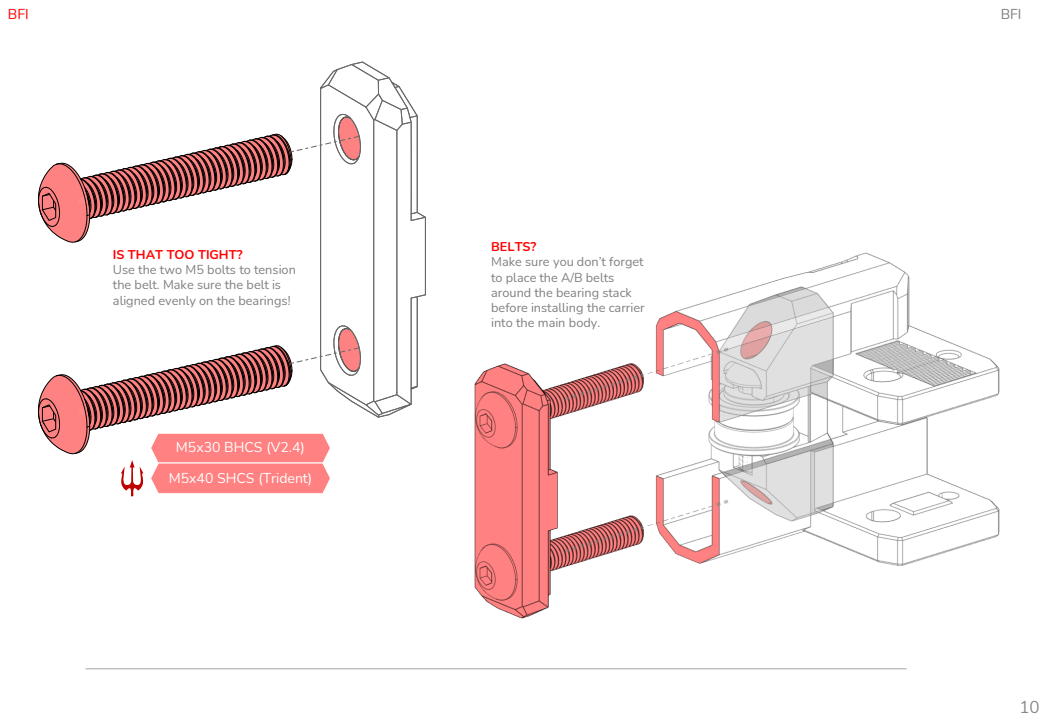
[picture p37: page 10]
BFI; M5x30 BHCS (V2.4); M5x40 SHCS (Trident)

BELTS?
Make sure you don’t forget
to place the A/B belts
around the bearing stack
before installing the carrier
into the main body.

IS THAT TOO TIGHT?
Use the two M5 bolts to tension
the belt. Make sure the belt is
aligned evenly on the bearings!

BFI | BFI

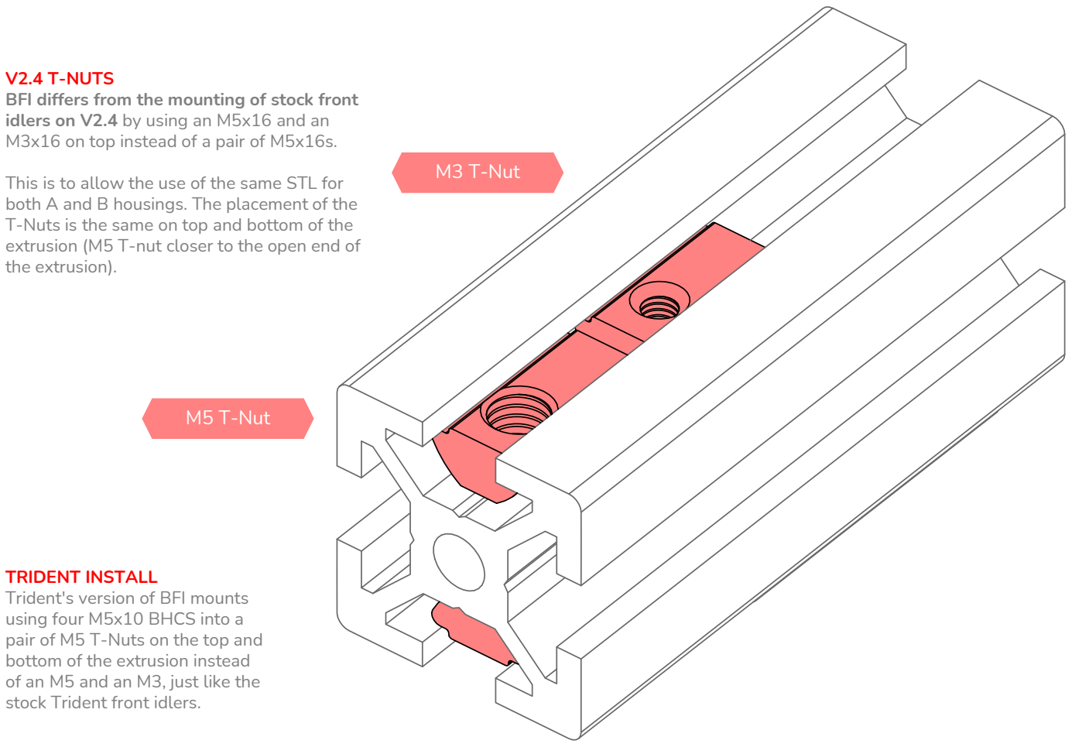
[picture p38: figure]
M5 T-Nut; V2.4 T-NUTS; idlers on V2.4 by using an M5x16 and an; the extrusion).; M3 T-Nut; TRIDENT INSTALL Trident's version of BFI mounts using four M5x10 BHCS into a pair of M5 T-Nuts on the top and bottom of the extrusion instead of an M5 and an M3, just like the stock Trident front idlers.

BFI differs from the mounting of stock front M3x16 on top instead of a pair of M5x16s. This is to allow the use of the same STL for both A and B housings. The placement of the T-Nuts is the same on top and bottom of the extrusion (M5 T-nut closer to the open end of

BFI

Z BELTS?
The top Z belt clamps are held down with an M5x16 BHCS and an M3x16 BHCS. The same part is used on the bottom for stock Z joints on a V2.4. If you are using non-stock Z joints (i.e. GE5C, Rockem Sockem, Rigid, etc.), it is recommended to use the bottom Z belt clamps that were included with the specific Z

CROOKED Z BELTS??
Double check where you have installed your Z belts. The belt should be up against the body of the idler before it goes under the clamp; the belt should only go through the “mouth” on the outer edge of the printer.

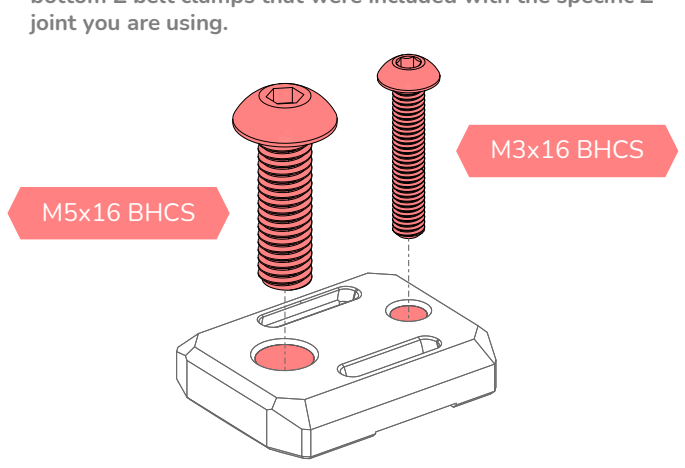
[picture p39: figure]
M5x16 BHCS; joint you are using.; M3x16 BHCS
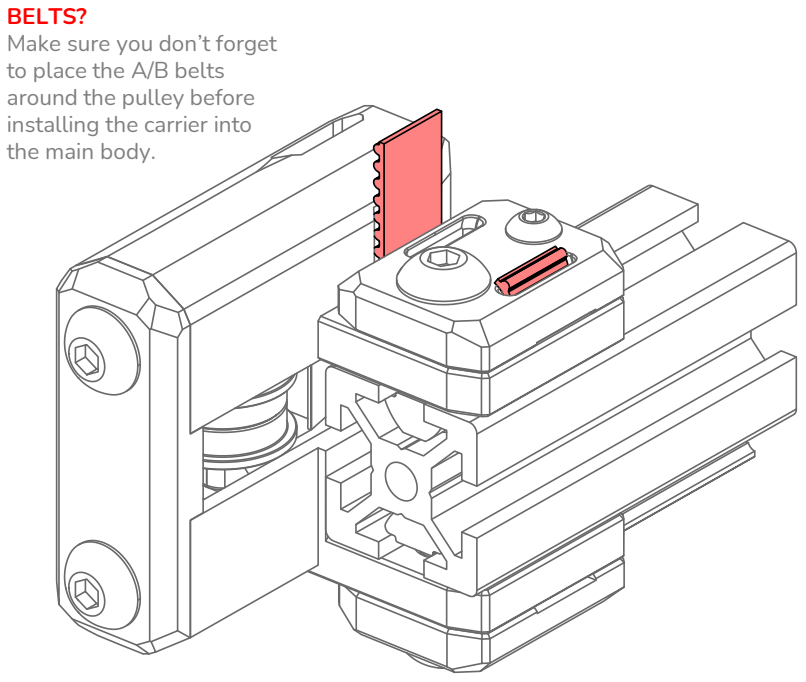
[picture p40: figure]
BELTS? Make sure you don’t forget to place the A/B belts around the pulley before installing the carrier into the main body.

WHAT ABOUT TRIDENT?
BFI for Trident uses two M5x10 BHCS on top, two more on bottom (on each side) but obviously Trident has no Z belt clamps to worry about. Unlike V2.4, there is no mounting hardware change from stock front idlers for Trident.

VERSION 2024.02.27

# BFI

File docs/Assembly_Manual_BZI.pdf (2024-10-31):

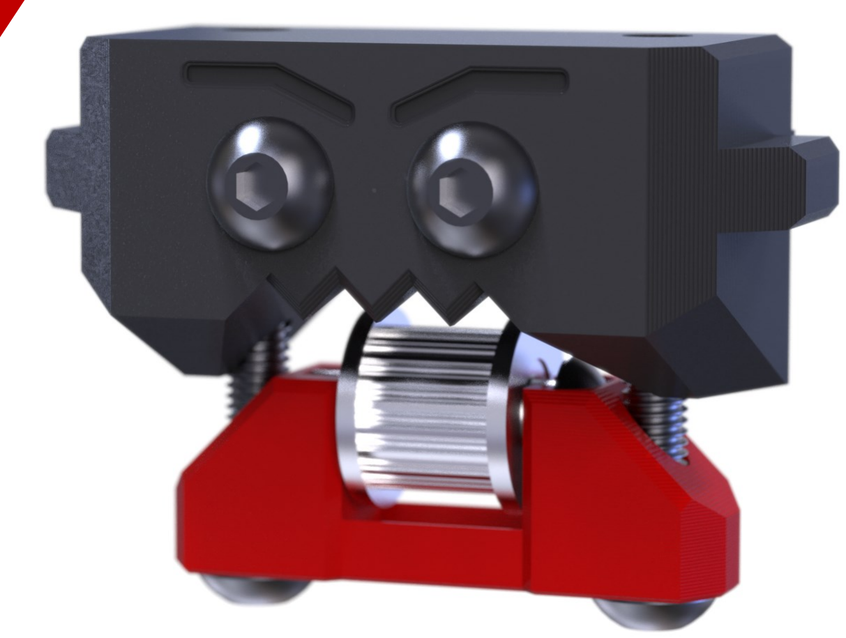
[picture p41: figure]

## VERSION 10/31/2024

# ASSEMBLY MANUAL

## Everyone could use a little extra Beef

# BZI

## STL FILE KEY

## PRINT GUIDELINES

### The STL naming convention used for BFI/BZI is the same as that used for VORON printers:

The recommended print settings are also those used for VORON printers:

## PRIMARY COLOR

### Example BZI_V2.4_idler_body_x4.stl These files will have nothing

at the start of the filename.

## ACCENT COLOR

### Example [a]_BZI_V2.4_carrier_x4.stl These files will have ‘’[a]’’ to the front to mention that they are intended to

be printed with an accent color.

## QUANTITY REQUIRED

### Example [a]_BZI_V2.4_carrier_x4.stl If a file ends with ‘’_x#’’, that is telling you the quantity of that part required to build this

system..

## FDM MATERIAL

Micron was designed for ABS.

### Use other plastics at your own

discretion.

## LAYER HEIGHT

### Recommended : 0.2mm

## EXTRUSION WIDTH

### Recommended : Forced 0.4mm

## INFILL PERCENTAGE

### Recommended : 40%

## INFILL TYPE

Grid, Gyroid, Honeycomb, Triangle, Cubic, Adaptive Cubic.

## WALL COUNT

### Recommended : 4

## SOLID TOP/BOTTOM LAYERS

### Recommended : 5

## SUPPORTS REQUIRED

### If the part needs supports, they are

built into the model.

INTRODUCTION | BZI

### HOW TO GET HELP

DISCO? OH …DISCORD
If you need assistance with your BFI/BZI assembly, you can head over the Voron Discord server and post your questions ( typically in the #voronuser_mods channel ).

GIT GUD
If you want to stay up to date on the latest files for BFI/BZI. The github page is the only source for the latest files.
HARDWARE - REFERENCES | BZI

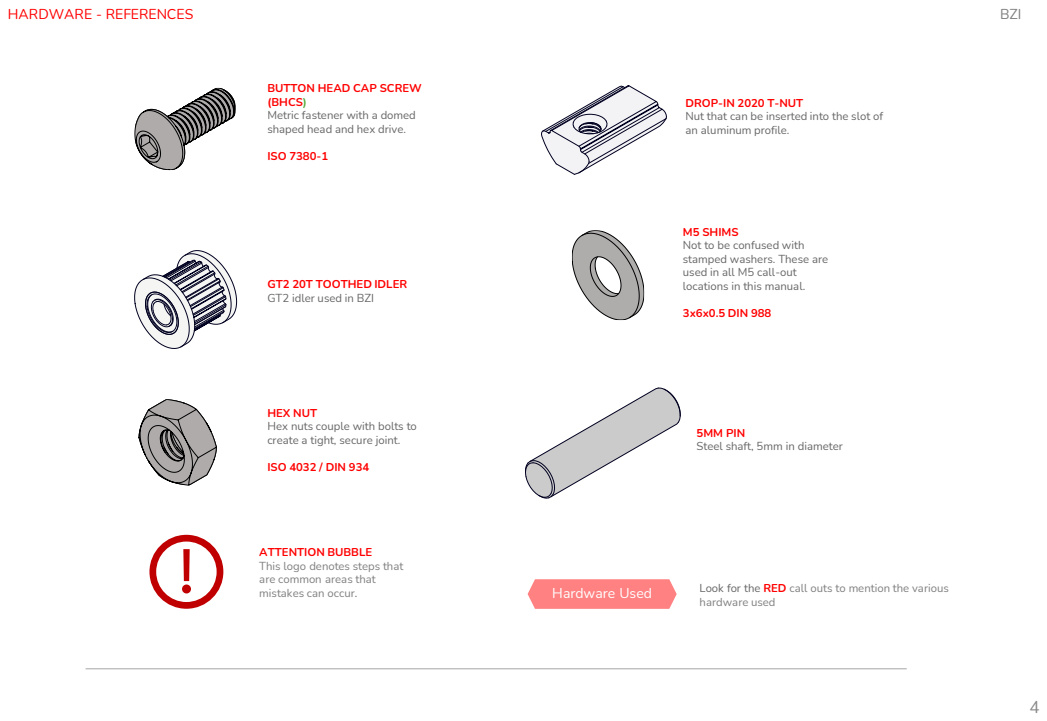
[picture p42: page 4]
HARDWARE - REFERENCES; BZI; mistakes can occur.; Hardware Used; Look for the RED call outs to mention the various; hardware used

BUTTON HEAD CAP SCREW
(BHCS)
Metric fastener with a domed
shaped head and hex drive.
ISO 7380-1

DROP-IN 2020 T-NUT
Nut that can be inserted into the slot of
an aluminum profile.

M5 SHIMS
Not to be confused with
stamped washers. These are
used in all M5 call-out
locations in this manual.
3x6x0.5 DIN 988

GT2 20T TOOTHED IDLER
GT2 idler used in BZI

HEX NUT
Hex nuts couple with bolts to
create a tight, secure joint.
ISO 4032 / DIN 934

5MM PIN
Steel shaft, 5mm in diameter

ATTENTION BUBBLE
This logo denotes steps that
are common areas that

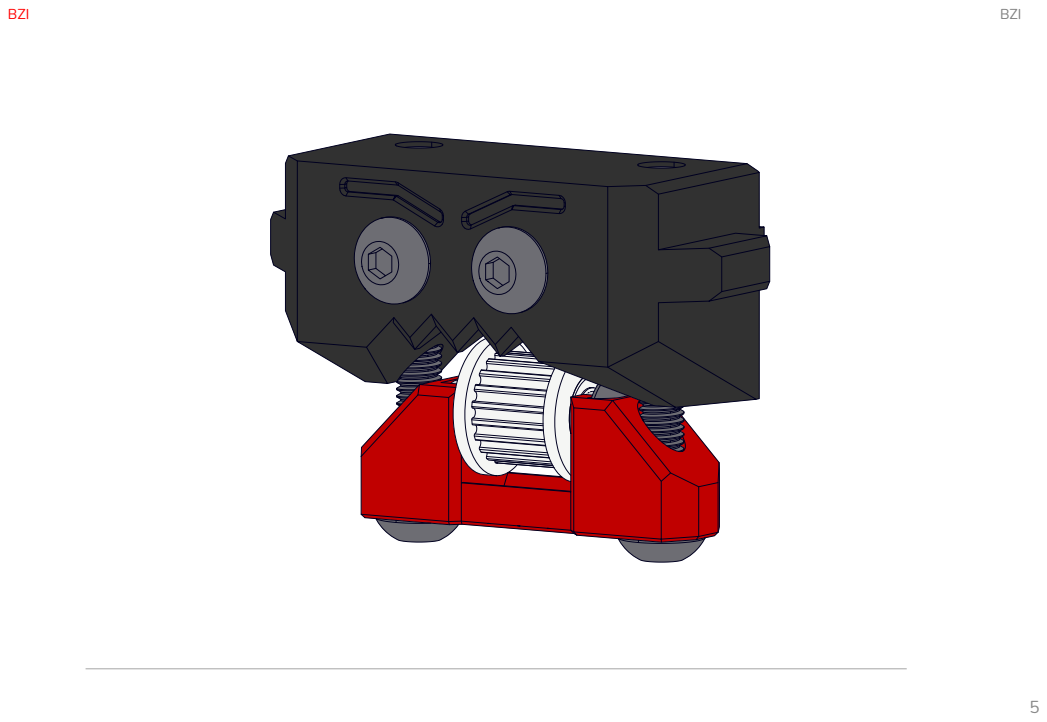
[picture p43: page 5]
BZI

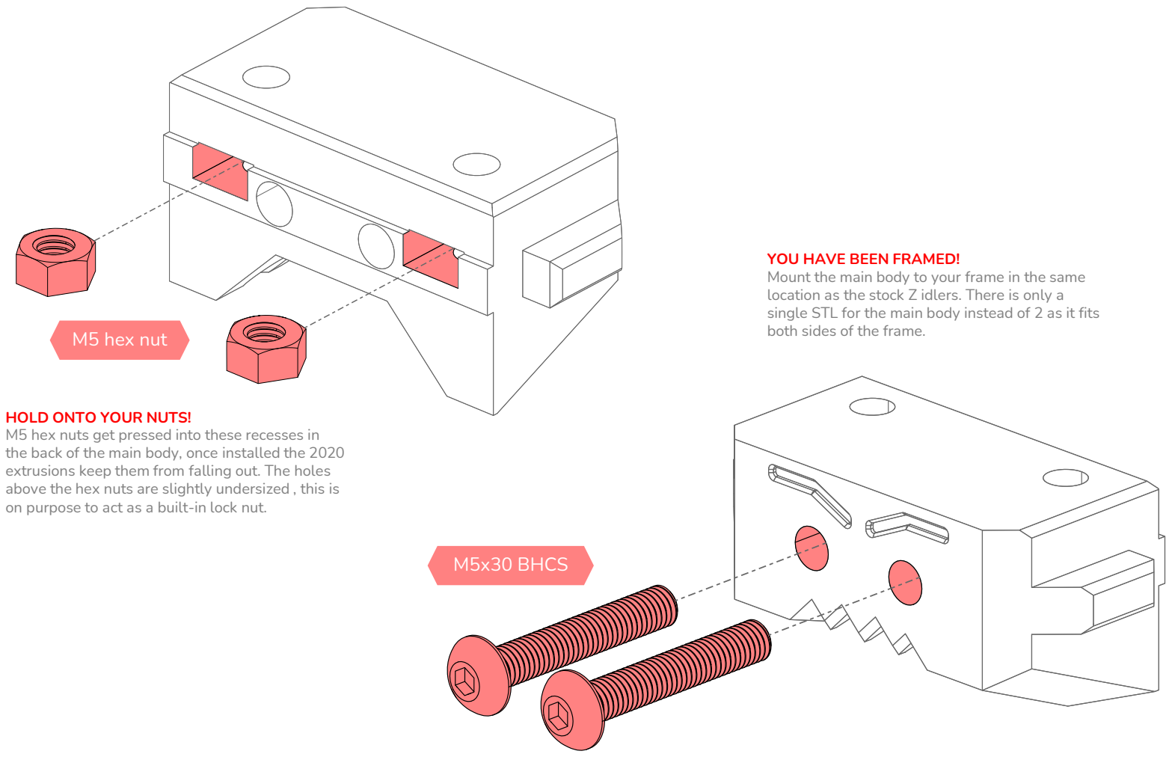
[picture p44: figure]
M5 hex nut; HOLD ONTO YOUR NUTS!; M5x30 BHCS; YOU HAVE BEEN FRAMED!; both sides of the frame.

M5 hex nuts get pressed into these recesses in the back of the main body, once installed the 2020 extrusions keep them from falling out. The holes above the hex nuts are slightly undersized , this is on purpose to act as a built-in lock nut.

Mount the main body to your frame in the same location as the stock Z idlers. There is only a single STL for the main body instead of 2 as it fits

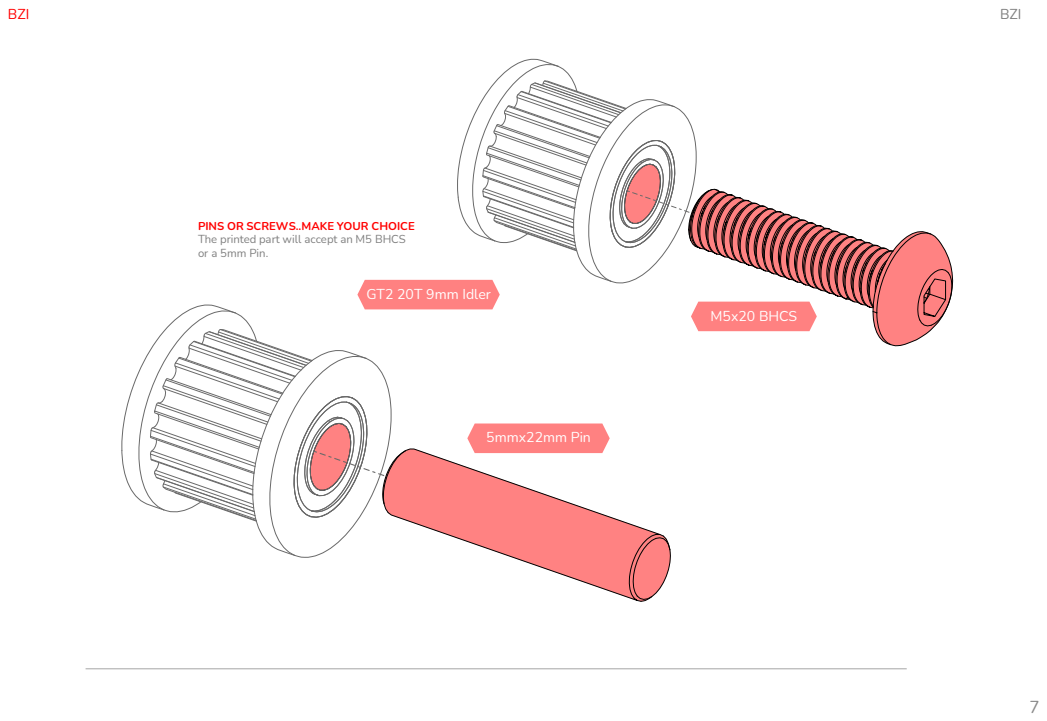
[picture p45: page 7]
M5x20 BHCS; 5mmx22mm Pin; GT2 20T 9mm Idler

PINS OR SCREWS..MAKE YOUR CHOICE
The printed part will accept an M5 BHCS
or a 5mm Pin.

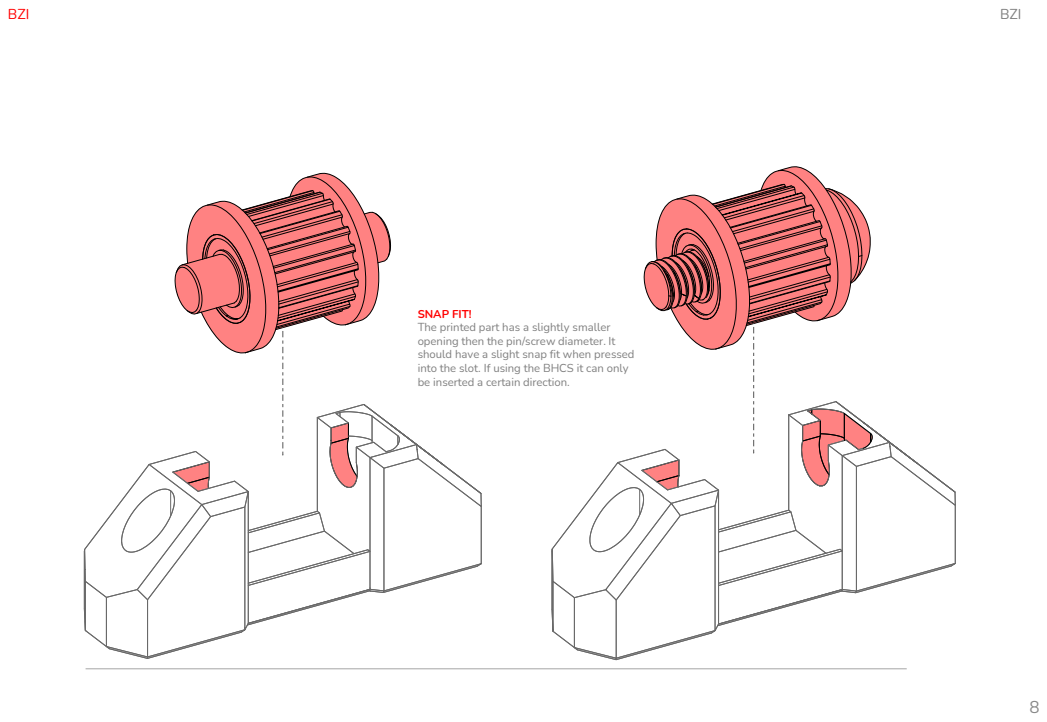
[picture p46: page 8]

SNAP FIT!
The printed part has a slightly smaller
opening then the pin/screw diameter. It
should have a slight snap fit when pressed
into the slot. If using the BHCS it can only
be inserted a certain direction.

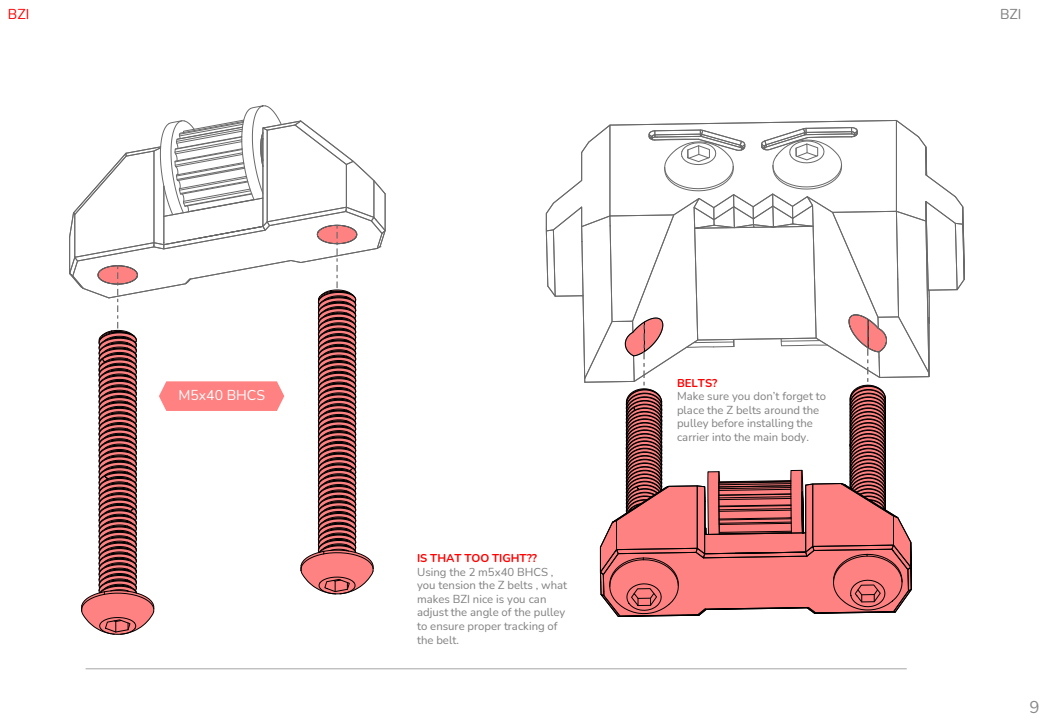
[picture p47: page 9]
M5x40 BHCS

BELTS?
Make sure you don’t forget to
place the Z belts around the
pulley before installing the
carrier into the main body.

IS THAT TOO TIGHT??
Using the 2 m5x40 BHCS ,
you tension the Z belts , what
makes BZI nice is you can
adjust the angle of the pulley
to ensure proper tracking of
the belt.

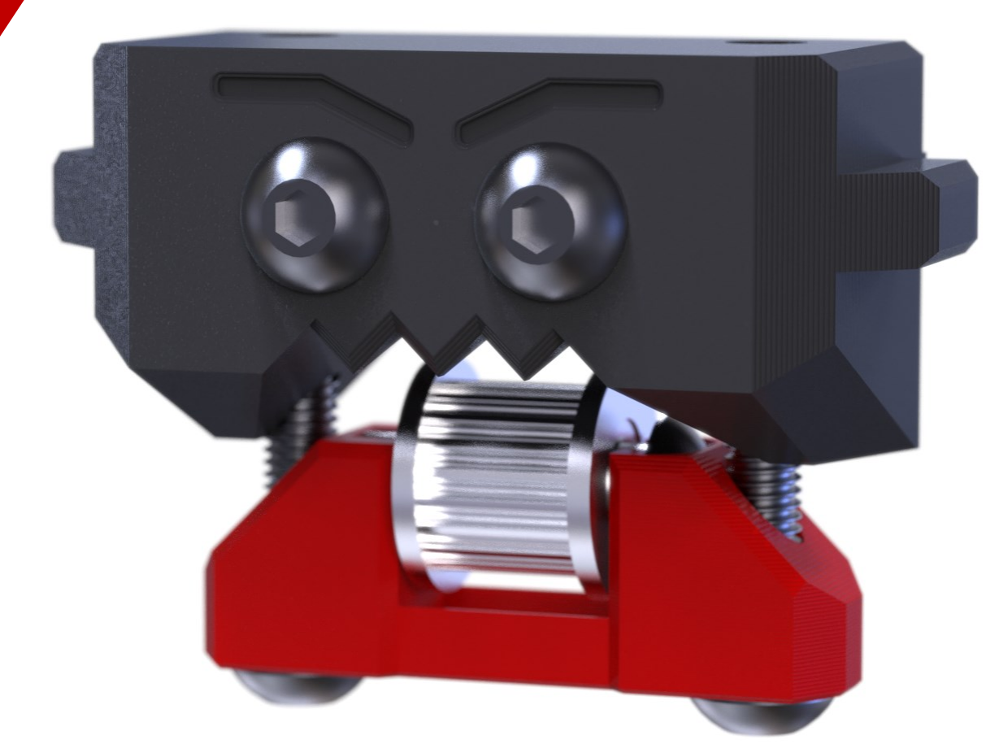
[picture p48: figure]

## VERSION 02/15/2024

# BZI

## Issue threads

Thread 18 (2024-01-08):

STL Fix ?

ggrigon, 2024-01-08:
[BFI_Front_with_logo_M3_symetrical_x2.stl](https://github.com/clee/VoronBFI/blob/main/usermods/Tetsu/Symetrical%20BFI/STLs/BFI_Front_with_logo_M3_symetrical_x2.stl)

The included STL is without logo

clee, 2024-01-11:
@tetsu97!

Closed 2024-02-24.

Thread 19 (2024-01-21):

BOM for BZI for V2.4: minor error about bolts head

RicRavGithub, 2024-01-21:
In BOM list of BZI for Voron 2.4 you declare
8× M5×40 **S**HCS
But looking at images, CAD file and real printed parts, it seems that
8× M5×40 **B**HCS
are instead the right choice.
Btw, it's not the optimal solution, but works also with socket head cap screw.

pajmannen, 2024-04-10:
I noticed this too just now!

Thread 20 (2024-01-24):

Symmetrical Mod Minor Issues

ndanyluk, 2024-01-24:
Hi Clee, love the BFI parts, already assembled before I saw the symmetrical parts and was going to reprint.  Couple of things I noticed:

* Parts aren't oriented for printing - the housing for example is oriented as they would be assembled on the printer, not face down like the standard BFI parts
* STLs aren't labelled as [a] for accent like the standard BFI parts
* Standard BFI parts use 5x18mm pins with optional BHCS - this mod only supports M3 or M5 BHCS with no option for pins
* Symmetrical Mod isn't listed in the Mods ReadMe with a description like the other mods

Going to see if I can get a PR going with at least the first 2 items updated.  I'll try my hand at the 3rd as well, but my CAD skills are a bit weak in this department

orangetruth, 2024-02-12:
Also BFI_Front_with_logo_M3_symetrical_x2.stl doesn't actually have a logo

Closed 2024-02-25.

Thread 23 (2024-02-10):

Assembly instructions missing

kozross, 2024-02-10:
While there is a detailed list of additional required parts, there are no instructions on how to build these.

clee, 2024-02-10:
Yeah, assembly instructions are on my TODO list, but thanks for making an issue to track it!

kozross, 2024-02-10:
FWIW, [this video (at the linked timestamp)](https://www.youtube.com/watch?v=XtfESO4ALw8&t=970s) shows the assembly process. If you don't think it's wrong somehow, you could link to it in the interim?

cjohnson-phys, 2024-02-24:
I think I am most confused about the belt clamps when upgrading from the default v2.4 belt clamps. Any pointers?

roykrikke, 2024-04-21:
Any status update?

messymouse, 2024-06-21:
I made an exploded view for BZI, which is pretty much all the instructions needed for these. I don't know how to do the fancy PDF files (I would love to learn!) but I hope this helps =)

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

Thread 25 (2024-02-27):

Symmetrical BFI Housing for VT has the wrong screw holes

orangetruth, 2024-02-27:
[BFI-VT_Housing_Symmetrical_x2.stl ](https://github.com/clee/VoronBFI/blob/main/usermods/Tetsu/Symetrical%20BFI/STLs/) has an M5 and an M3 hole on each side like the V2.4 housing, but the VT housing should have four M5 holes.

orangetruth, 2024-03-02:
Actually the entire VT housing is the 2.4 housing - it won't fit M3x40s. The step file doesn't have the correct VT components either. I suggest removing the trident version completely for now so others don't run into the same issues I have when trying to use this mod.

MarkusFelix, 2024-03-15:
I've just pushed a little change to the housing for Trident #26 - should fix the mounting screw and z-belt situation

dougshell, 2024-04-14:
any follow up on this?

clee, 2024-06-05:
Sounds like @tetsu97 needs to make some updates

Person1873, 2024-08-03:
While this is 100% correct. I don't really see it as a problem?

Just use replace the T nuts with m3 and use some m3x8 screws.
Most voron kits come with an excess of both.

orangetruth, 2024-08-05:
@Person1873 I updated the title since that was probably causing some confusion. BFI-VT_Housing_Symmetrical_x2.stl is using the v2.4 housing. It's a bigger issue than just the wrong screw holes. It's the wrong part.

Person1873, 2024-08-05:
> @Person1873 I updated the title since that was probably causing some confusion. BFI-VT_Housing_Symmetrical_x2.stl is using the v2.4 housing. It's a bigger issue than just the wrong screw holes. It's the wrong part.

I've just reviewed the files & this is incorrect.
The VT housing does not include a pass through for the 2.4 Z belts.

I'm running the most up to date m3 variant of these parts without issue.

orangetruth, 2024-08-08:
@Person1873 Sorry if I wasn't clear enough. Here are some pictures to clarify:
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
A V2.4 housing with the z belt hole filled in does not make it a VT housing. The symmetrical VT housing only fits M5x30s, not M5x40s per the VT BFI BOM.

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
The VT housing also doesn't have the belt pattern.

Hopefully these pictures make it clear that the symmetrical VT housing was based off the standard V2.4 housing, not the standard VT housing.

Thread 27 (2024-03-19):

V2.4 Symmetric BZI Idler Body may interfere with certain LED strip mounts

louisrousseau, 2024-03-19:
The 5 mm-or-so "ear" on both sides is really needed on one only - note the stock "Z Tensioner Bracket" A and B styles -  and in my specific installation collided with an LED strip mount.

That plus an unrelated brim setting mixup (had internal enabled - no eyebrows!) led me to slice these after a quick hop in OnShape:

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

clee, 2024-06-05:
Hey, thanks for the bug report!

> The 5 mm-or-so "ear" on both sides is really needed on one only

Yeah, having them on both sides is purely so that we only need one STL that you can print 4 of. But this comes with some possible downsides. If you submit a BZI usermod I'd be happy to accept it! And I'm not completely closed to the idea of changing the main BZI housings, but I'd like to see how it works out for folks as a usermod first.

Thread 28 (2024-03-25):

BZI v2.4 Carrier too snug

Nomsplease, 2024-03-25:
The BZI carrier for the Voron 2.4 is too snug on my 9mm idlers that were used in my stock Z idlers.

These were sourced a long time ago so this may be a non-issue now. My Idlers are 14.06mm wide and the current carrier printed at 14.09mm. They do fit but are way too snug to move.

I modified the CAD to make one that has a 15mm wide opening for the idler instead of 14mm. The CAD shows the idler is 13mm wide, so I went with 1mm over the size of the idler. I am uploading a ZIP file with the STL and the quickly/crudely done STEP file incase anyone else might need it.

~~I am currently printing this and will validate it works for mine, I will cross this out once I confirm it works for my idlers.~~
They fit just as they should.

[14mm Carrier.zip](https://github.com/clee/VoronBFI/files/14746500/14mm.Carrier.zip)

Carl-Wilhelm, 2024-05-03:
Thank you. Same problem here with the idlers that came with my LDO kit.

clee, 2024-06-05:
Did you try the usermod specifically designed for this? https://github.com/clee/VoronBFI/tree/main/usermods/LillianaMirrors/

Nomsplease, 2024-06-05:
> Did you try the usermod specifically designed for this? https://github.com/clee/VoronBFI/tree/main/usermods/LillianaMirrors/

I didnt see these in the repo at the time. I have been running mine for a while without issue but I dont think we need a duplicate mod here. We can just close this up since it will stay here if its ever needed.

Closed 2024-06-05.

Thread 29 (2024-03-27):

Belt moves over the idler

aytact, 2024-03-27:
Hi, there is an issue with idler carrier. Belt moves over idler in direction of z+.

What may cause this issue. Belt is brand new.

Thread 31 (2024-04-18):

Design allows fools like me to pinch the belt and break parts everywhere on my Micron Plus

midmadn, 2024-04-18:
Design allows fools like me to pinch the belt and break parts everywhere on my Micron Plus trying to figure out why my gantry is clicking and binding and moving hard.
Not knowing CAD - my only fix was to cob them up in OrcaSlicer with added in parts that prevent this again. Someone knowing CAD could do something much nicer.
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

midmadn, 2024-04-18:
Total height from build plate to the top of the rectangular pegs I added is 16mm. If anyone cares.

clee, 2024-06-05:
You should submit your altered carriers as a usermod!

midmadn, 2024-06-05:
Hi Clee and thank you for all you do for us less knowledgable 3d printer geeks. I was really hoping you or someone that knows CAD would run with my fix/idea. It's your part and design. I'm just offering a change idea to help people that make foolish mistakes like me. Please feel free to use my idea or any part of it if you choose. It's your cool mod. If I can help to make it even a touch better or more foolproof - that makes me happy.

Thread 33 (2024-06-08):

(Minor) BHCS vs 5mm Pin options

HiTekCowboy, 2024-06-08:
In readme for 2.4/Trident, state "5x18MM dowel pin" OR "M5x16 BHCS" as **_options_**. for BFI.
Would provide clarity(and prevent impatient Americans from going on hardware store boondoggles for metric dowels).

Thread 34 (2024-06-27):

BZI are modeled with non-gates idler dimensions

jmeier5261, 2024-06-27:
Seen a few folks mention rubbing on BZI for 2.4 and Doom...never thought anything of it but i have been chasing a persistent z issue that only manifests on my DoomCube with very tiny z moves like a .2mm z hop. After rebuilding and replacing every component in my Z motion system I eventually realized that the rubbing on the Z idlers is very likely the cause.

The issue is that the Z idlers for 2.4 and Doom are modeled using a 9mm idler width of 13mm, however gates idlers are 14mm end to end
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

In the CAD I can see the opening itself is exactly 14mm because it is expecting the idler to be 13mm which is not correct.

I cant say for sure but I think a majority of Z idlers used are modeled after the dimensions of gates idlers. This causes rubbing and binding if the parts are not sanded.

clee, 2024-07-11:
@hartk1213 how could you do this to us

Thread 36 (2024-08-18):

BZI V2.4 carrier wrong stl file after last commit?

spaceman-nld, 2024-08-18:
It seems that during the last commit of file [a]_BZI_V2.4_carrier_x4.stl in the BZI V2.4 folder the wrong file was used. The stl has a large rectangular hole on one side of the pin cutout. The older file before the commit didn't have this and I don't think there is a reason the cutout should be there. The cutout seems exactly the same as the Doom carrier (also exact same file size) so I think a small error was made uploading the new BZI V2.4 carrier file.

asychev, 2025-06-25:
I can confirm

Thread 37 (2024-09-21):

Mounting (Symetrical) BFI, M3x16's?

Steiner-SE, 2024-09-21:
I'm slightly confused installing my symetrical BFIs as the BOM states 2x M3x16 NHSC, my hardware kit comes with 3, but it seems 4 are needed?
You place M5 and M3 t-nuts top and bottom, and there are holes for them in the housing, for two sides, that's 4 M5x16 and 4x M3x16.
What holes should be empty, should both M3 t-nuts not be placed on the bottom?

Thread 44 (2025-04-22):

BZI carrier interferes with flange on Powge 9mm 20T idler

BildermanKawasaki, 2025-04-22:
The Powge 20T flange has a diameter of 18mm. I'm guessing the genuine Gates flange is a bit smaller.

BildermanKawasaki, 2025-04-22:
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

BildermanKawasaki, 2025-04-22:
[a]_BZI_V2.4_carrier_x4.stl is the specific file I printed.

BildermanKawasaki, 2025-04-23:
I have a redesigned part that extends the bottom of the carrier down 2mm and moves the top of the center portion down 2mm that works great for the powge idler. I can create a PR for a user mod or just upload the file here for y'all to do with as you please.

BildermanKawasaki, 2025-04-23:
[Pull request #45](https://github.com/clee/VoronBFI/pull/45) created with working fix.

BildermanKawasaki, 2025-05-01:
I feel really silly, but this issue is not an issue. I was trying to use the idler for the xy joints instead of the bearings that belong there. Sorry for wasting anyone's time that may have looked at this.

Closed 2025-05-01.

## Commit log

2023-06-07 initial BFI release candidate
    [BFI-Micron-Carrier.stl, BFI-Micron-Front.stl, BFI-Micron-Housing.stl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]
2023-06-08 update V2.4 housing (thanks @KayosMaker!)
    [BFI-V2.4-A-Housing.stl, BFI-V2.4-B-Housing.stl, BFI-V2.4-Housing.stl]
2023-06-09 Use Voron conventions for STL filenames
    [BFI-Micron_Housing_x2.stl, BFI-SaladFork_Housing_x2.stl, BFI-V2.4_Housing_A_x1.stl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]
2023-06-09 Pull in changes from @hartk1213
    [BFI-Micron_Housing_x2.stl, BFI-SaladFork_Housing_x2.stl, BFI-V2.4_Housing_A_x1.stl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]
2023-06-13 Add Beefy Z Idlers (thanks @KayosMaker and @hartk1213)
    [BZI_Doom-carrier_x4.stl, BZI_Doom-idler_A_x2.stl, BZI_Doom-idler_B_x2.stl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]
2023-06-13 Use Voron conventions for BZI STLs
    [[a]_BZI_Doom-carrier_x4.stl, [a]_BZI_Micron-carrier_x4.stl, [a]_BZI_V2.4-carrier_x4.stl]
2023-06-13 README.md: clarify bearing stack instructions
2023-07-28 Updated the front idler belt clamp, added AB drives belt clamp
    [[a]_BFI-V2.4_Belt_Clamp_x2_AB_Drives.stl, [a]_BFI-V2.4_Belt_Clamp_x4.stl]
2023-08-03 Add BZI for Micron Pins Mod (#3)
    * Add files via upload
    * Create Usermods Table
    * Create Usermods Table
    * Delete usermods/Jadecky/STLs/Non Symetrical Bodies directory
    * Add files via upload
    * add Usermods
    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
    [(a)_Idler_Carrier_Pin_Mod_x4.stl, BZI_Micron_Pin_Mod.step, Idler_Body_L_x2.stl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]
2023-08-05 Add files via upload
    Create Usermods Table
    Create Usermods Table
    Delete usermods/Jadecky/STLs/Non Symetrical Bodies directory
    Add files via upload
    add Usermods
    add BZI for Micron Pins Mod
    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
    [BFI_Micron_Pin_Mod.step, Idler_Body_L_x2.stl, Idler_Body_R_x2.stl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]
2023-08-17 Usermod for allowing wider pulleys to be used.
    [BZI 2.4 for 14mm Idlers.3mf, BZI-Chaoticlab Idlers V2.4.step]
2023-08-17 fixed minor pathing issues
    [BZI 2.4 for 14mm Idlers.3mf, BZI-Chaoticlab Idlers V2.4.step]
2023-08-22 Added missing BOM for 2.4
2023-08-22 Added DoomCube 4040 variant.
    [BZI_DoomCube_4040_Idler_Body_A.stl, BZI_DoomCube_4040_Idler_Body_B.stl, BZI_Doomcube_4040 v4.f3d]
2023-08-23 Added Z belt clearance slot for BFI-V2.4
    [BFI-V2.4_Housing_x2.stl]
2023-09-08 V2 and Micron Housing fixes to make them more printable
    [BFI-Micron_Housing_x2.stl, BFI-V2.4_Housing_x2.stl, [a]_BFI-Micron_Front_x2.stl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]
2023-09-08 various changes to V2, VT and Micron BFI/BZI
    Micron
    - Updated BZI carrier and idler housing , had to move tensioner screws apart to allow use of m3x16 shcs for the bearing axle
    V2
    - Added a new carrier option that allows the user to use an m5x16 BHCS for the BFI and an M5x20 BHCS for the BZI for V2
    VT
    - Added a new carrier option that allows the user to use an m5x16 BHCS for the BFI
    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
    [BZI_Micron-idler_x4.stl, Micron_BZI_CounterSunkSpacer.stl, Micron_BZI_CounterSunkSpacer_MMU.stl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]
2023-09-16 BZI Light - Usermod by Mosher (#12)
    Add Mosher's BZI usermod
    [Carrier countersunk M3 for 20mm shaft x4.stl, Carrier countersunk M3 for 22mm shaft x4.stl, Carrier for 20mm shaft x4.stl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]
2023-10-08 Update README.md to the Correct BOM for ANT printers (#14)
    * Update README.md
    Updated for the Micron and Salad Fork.
2023-10-08 Added Smooth BFI for V2.4 (#15)
    * Added Smooth BFI for V2.4
    * Added witness marks
    Witness marks make it easier to visually ensure that the bearing in the tensioner is properly aligned with the belt path
    [BFI-V2.4 Smooth.step, [a]_belt_clamp_a_x2.stl, [a]_belt_clamp_b_x2.stl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]
2024-01-06 Modified version of telxoid usermod to using M3 fasteners and heat inserts (#17)
    * Create AMFkuna
    * Delete usermods/AMFkuna
    * Create Readme.md
    * Update Readme.md
    * Update Readme.md
    * Update Readme.md
    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
    [BFI_V2_VT_Front_Logo M3.stl, BFI_V2_VT_Grippy_Carrier M3.stl]
2024-01-06 Add tetsu97's Symmetrical BFI usermod (#16)
    [BFI Symetric.step, BFI-V2.4_Housing_symetrical_x2.stl, BFI-VT_Housing_symetrical_x2.stl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]
2024-01-30 add @MikeYankeeOscarBeta's V2.4 9mm BFI usermod (#21)
    initial version of 9mm BFI for V2.4
    [V2_BFI_Front_Cover _9mm_Belt_v1_x2.stl, V2_BFI_Front_Idler_5mmPin_9mm_Belt_v1_x2.stl, V2_BFI_Housing_9mm_Belt_v1_x2.stl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]
2024-02-24 Symmetrical Mod Fixes and Updates (#24)
    * Fix naming of Symmetrical BFI STLs
    * [Symmetric BFI] Add Logo Parts
    * [Symmetric BFI] Add 5x18 Pin Carriers
    * [Symmetric BFI] Update CAD
    * [Symmetric BFI] Re-orient parts for printing
    * [Symmetric BFI] Update usermods readme
    [BFI Symetric.step, BFI-V2.4_Housing_Symmetrical_x2.stl, BFI-V2.4_Housing_symetrical_x2.stl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]
2024-05-14 Added User Mod - 45 Degree Housing. (#32)
    * Added 45degree User Mod
    makes the housing a bit easier to print without changing anything major.
    * updated photo
    broken photo link
    * Updated print orientation of STL
    [45d-V2.4_Housing_x2.stl.stl, BFI V2.4 better printability 45 degree.step, [a] 45d-V2.4_Belt_Clamp_x4.stl.stl]
2024-07-11 fixed #34 , and changed the hole diameter on the BZI on top to a smaller diameter to act as a nylock nut after the m5 hex nut to help prevent the m5s from backing out on BZI , updated Micron BFI/BZI 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
    [BFI-Micron_Housing_x2.stl, BFI-SaladFork_Housing_x2.stl, BFI-V2.4_Housing_x2.stl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]
2025-01-10 Fix symetrical -> symmetrical typos; correct VT housing body by removing belt clamps and restoring original flanges/m5 holes for mounting
    [BFI Symmetric.step, BFI-V2.4_Housing_Symmetrical_x2.stl, BFI-VT_Housing_Symmetrical_x2.stl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]
2025-01-10 add missing chamfer on housing
    [BFI Symmetric.step]
